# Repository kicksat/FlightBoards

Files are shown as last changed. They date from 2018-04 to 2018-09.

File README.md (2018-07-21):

# mainboard
<p align="middle">
Main PCB driving the Kicksat-2 cubesat mothership. Its job is to depoly Sprites, which looks kind  of like this:
  </br>
</br>
Benchtop development hardware looks like this:
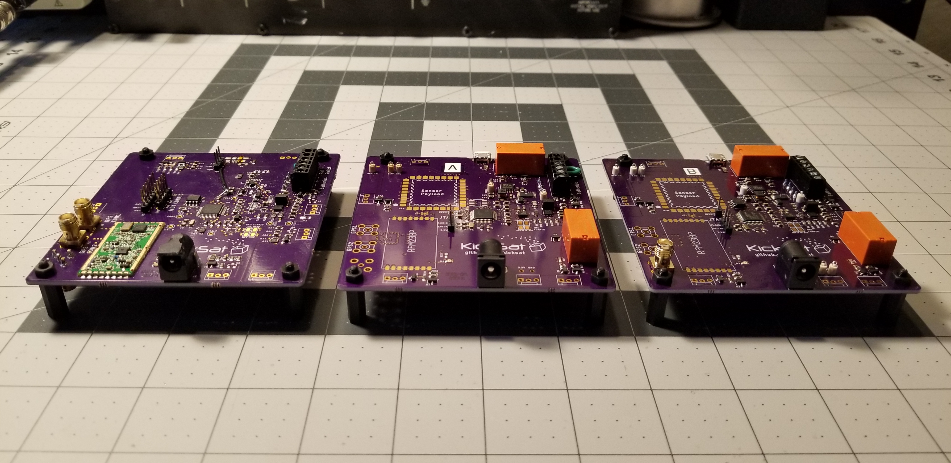
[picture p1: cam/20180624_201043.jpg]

</p>

# License

[Creative Commons Attribution-ShareAlike 4.0 International](https://creativecommons.org/licenses/by-sa/4.0/)

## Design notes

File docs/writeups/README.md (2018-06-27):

## Burnwire hardware block diagram
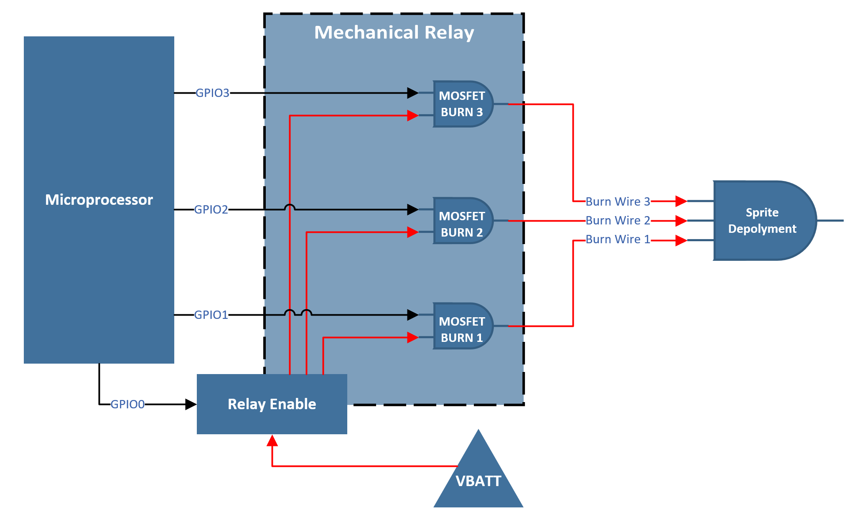
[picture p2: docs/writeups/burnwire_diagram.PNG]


## Burnwire schematic diagram
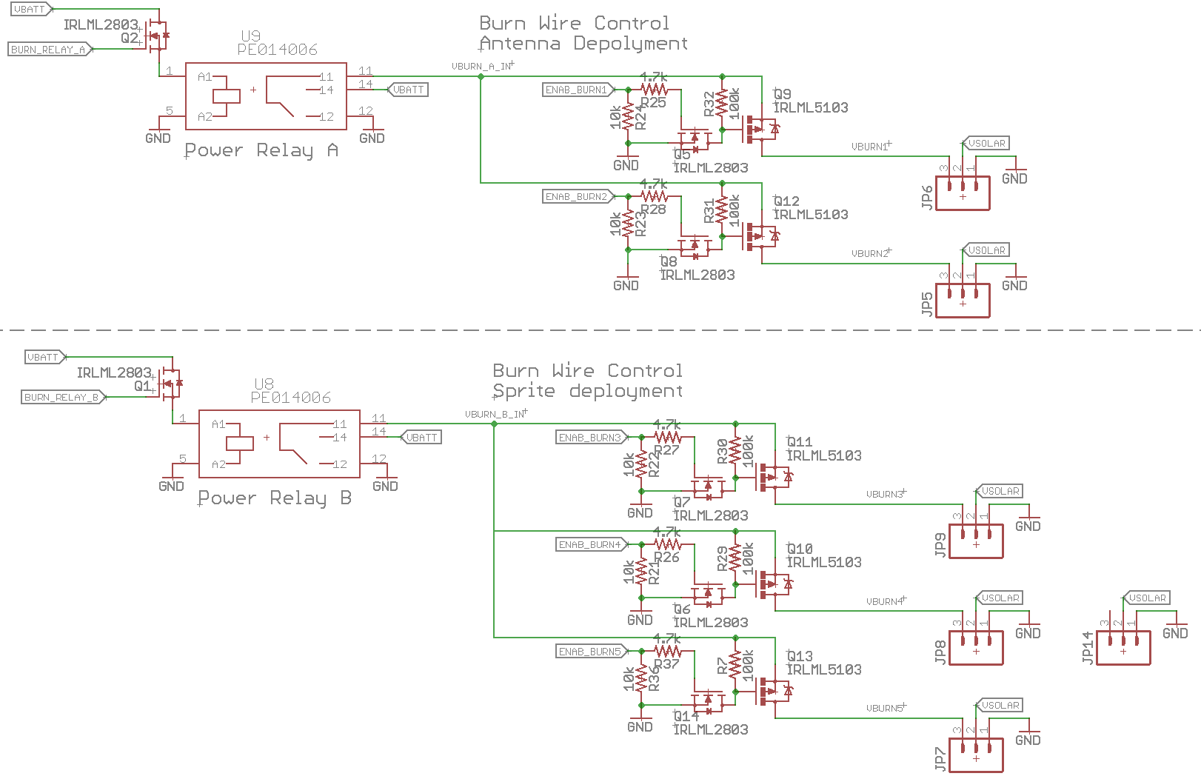
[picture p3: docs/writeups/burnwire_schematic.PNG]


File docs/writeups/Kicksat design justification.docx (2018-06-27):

Kicksat-2 Design Architecture

Radiation Evaluation

Kicksat-2 hardware was designed with a “careful COTS” methodology to ensure mission requirements while optimizing lifetime, capability, and component cost/availability. This approach leverages existing component radiation testing literature with detailed environmental modeling to drive IC component selection.

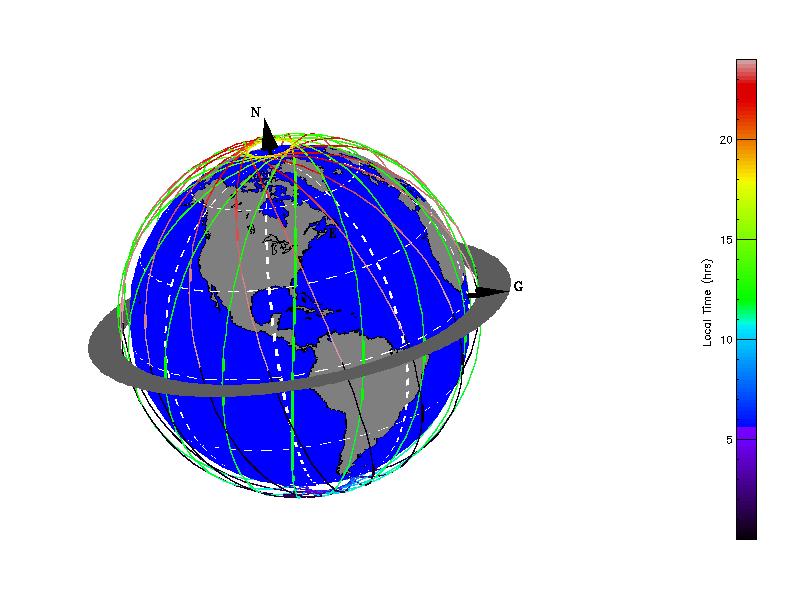
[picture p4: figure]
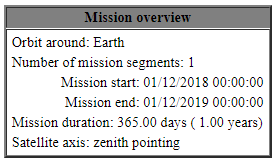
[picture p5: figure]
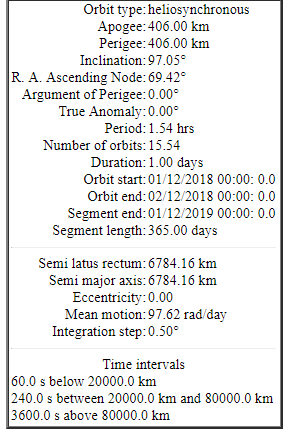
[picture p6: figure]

Environment Simulation:

Figure 1

The ESA Space ENVironment Information System (SPENVIS) was used to generate high-level orbital parameters and subsequent radiation models. Further analysis was then performed using raw AE9/AP9 data in conjunction with Geant4, COMSOL, and VisualTCAD tools to model the anticipated radiation effects. Relevant SPEVIS input parameters used in orbital generation, and a graphical representation of a 24 hour orbital path are shown in Figure _____.

Using the parameters from Figure ____, a standalone copy of AE9/AP9 v1.50 was used to generate trapped particle data. Kicksat-2 mission altitude dictates that total ionizing dose (TID) accumulation will predominately come from trapped particles (electrons and protons). Single event effects (SEE), however, must still be considered since Kicksat-2 must not allow premature Sprite deployment.

Table I | Integrated Circuit Component Summary

P/N | Manufacturer | Function | Mission Critical? | Flight Heritage? | Radiation Test Data?
IRLML2803 | Infineon | N-channel MOSFET | Yes | Unknown | Yes
IRLML5103 | Infineon | P-channel MOSFET | Yes | Unknown | Yes
MAX706R | Maxim | Watchdog Timer | Yes | Yes | Yes
TPS54226 | TI | Regulator | Yes | Yes | Yes
RFM23BP | HopeRF | Radio Transceiver | Yes | Yes | No
MR25H40 | Everspin | Nonvolatile Memory | Yes | Yes | Yes
ATSAMD21G-A | Microchip | Microprocessor | Yes | Unknown | No
PE014006 | TE Connectivity | Mechanical Relay | Yes | No | No
S1216V8 | SkyTraq | GPS Module | No | Yes | No
LSM9DS1 | STMicro | IMU | No | Yes | No
MAX4372TEUK+T | Maxim | Current Sensor | No | Yes | No
LTC4121-4.2 | Analog Devices | Battery Charger | No | No | No
EP2W+ | Mini Circuits | RF Splitter | No | Unknown | No
TY1003 | Tyndall Works | Dosimeter | No | Yes | Yes

Discussion of Critical Components:

IRLML2803 & IRLML5103 – Power MOSFET

MOSFETs have well-documented electrical behavior in radiation environments. Incremental degradation due to ionizing radiation (TID) generally manifests as a decrease in gate threshold voltage for NMOS devices and an increase in threshold voltage for PMOS. Since discrete MOSFET devices play a critical role in the Kicksat burn-wire design, components with extensive radiation characterization were chosen and combined with multiple failsafes to ensure safe Sprite deployment.

Both the IRLML5103 and IRLML2803 were evaluated by O’Bryan et al. in 2001 for TID tolerance using the NSWC Crain facilities [XX]. Testing with the MIL-STD883 1019.8 procedure, including biased and unbiased conditions, the data shows the IRLML5103 has a TID tolerance greater than 35 krad, and the IRLML2803 greater than 30 krad. Both values far exceed the projected mission dose, and O’Bryan et al. has a strong testing track-record in the radiation effects community.

Device failure due to single event effects (SEE) such as burnout and latch-up are not relevant for the burn-wire design because the circuit sits dormant behind the mechanical relay circuit during nearly the entire mission. By protecting the burn-wire circuit with the mechanical relay, there is no bias across the MOSFET devices, thereby preventing an ionizing particle from creating parasitic effects within the channel/bulk regions and causing permeant damage.

MAX706R – Watchdog Timer

The MAX70X series of microprocessor supervisors have an extensive radiation test history covering TID, SEE, and SEL scenarios from a number of researchers [XX – XX]. As reported by Aaron et al, the MAX70X devices have a TID threshold of roughly 11 krad under worst-case biasing conditions [XX]. Additionally, Allen et al. reports a SEL threshold of 72 LET at 25C and about 68 LET at 85C. Both TID and SEE values are well within the required mission parameters, and failure of the MAX706R watchdog cannot result in the premature deployment of Sprites.

TPS54226 - Regulator

The TPS542XX family of DC-DC converters from Texas Instruments has been evaluated for TID and SEE tolerance by multiple researchers [XX – XX]. Specifically, Cochran et al. reported a TID tolerance of 15 – 20 krad, and Allen et al. reported no destructive SEL events occurring on devices biased at 10V or less and under a variety of temperature conditions. The efficiency of the TPS54226 device coupled the device behavior in radiation environments made it the most reliable choice for the Kicksat mission.

RFM23BP – Radio Module

The HopeRF RFM23BP module is a COTS radio integrated onto a PCB. Based on Silicon Labs’ Si4431 transceiver, which has known flight heritage, the module also contains BJT devices, a N-channel UHF amplifier, a SPDT switch, and an LDO [XX]. Although the flight heritage demonstrates adequate reliability for the Kicksat mission, PCB rework was performed to replace the LDO and SPDT switch with components with better documented radiation tolerance.

MR25H40 – Nonvolatile Memory

The MR25H40 is a 4MB non-voltage memory device constructed from magnetoresistive memory devices. The fundamental operation of magnetoresistive memory makes it inherently more tolerant to TID effects. Cochran et al. reports a TID tolerance of 90 – 100 krad during their 2007 work at Goddard Space Flight Center Radiation Effects Facility [XX]. Additionally, O’Bryan et al. was unable to observe upsets in the device using 89 MeV and 189 MeV protons during their 2007 work at the Indiana University Cyclotron Facility [XX].

The high radiation tolerance of the magnetic memory is used to store mission-critical parameters that are periodically verified and referenced during key mission objectives such as Sprite deployment and configurational backups for the microprocessor.

ATSAMD21G-A - Microprocessor

The Kicksat spacecraft operates from a Microchip SAMD2X family of microprocessor. Although there is no published literature on the radiation tolerance of this device, inferences can be made from Cochran et al., 2008 TID work on a “complex 65nm CMOS microprocessor” [XX]. Using the MIL-STD883 1019.8 test method, Cochran et al. reports no degradation detected up to the maximum tested level of 1000 krad. Furthermore, the ATSAMD21G device now has flight heritage after launching onboard OA-9 within the Brown Space Engineering EQUiSat 1U CubeSat.

The ATSAMD21G was chosen for the Kicksat mission because of its 32-bit ARM Cortex-M0+ architecture, low power consumption, and wide accessibility. The confidence level of the device to perform mission-critical duties was enhanced as described in the ______ section.

PE014006 – Mechanical Relay

The PE014006 relay was added to the design to provide an additional layer of protection from premature Sprite deployment. The power relay is inherently a mechanical device that can only be engaged when enough current is driven across the input terminals to actuate a mechanical switch. It therefore is not susceptible to TID degradation. The construction of the device employs a large isolation distance which also protects the relay from SEE-actuated events.

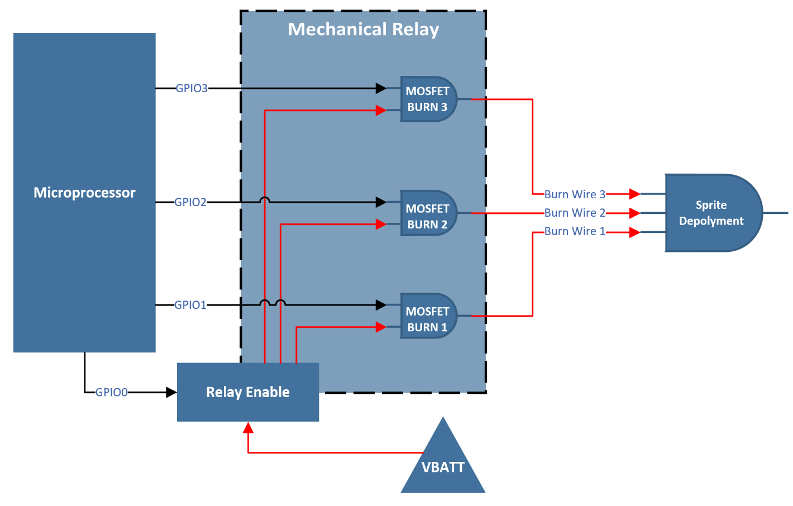
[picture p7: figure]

Sprite Deployment Scheme

Figure 2

The Kicksat-2 deployment scheme employs hardware and software safeguards to prioritize timely Sprite deployment above mission operational parameters, while also addressing detrimental environmental effects such as radiation-induced SEE and transient voltage spikes.

Hardware

Figure ___ and Fig. ____ illustrate the four hardware mechanisms in place to prevent premature deployment. A section of the schematic is also included in Fig. _____ as an alternative method of visualizing the safeguards. It’s important to note that each possible failure mode of the hardware defaults to a no-deployment condition. This hardware includes:

1. Three burnwires must be severed to release the Sprites.
2. Each burnwire circuit is operated by a separate I/O pin on the microprocessor.
3. A mechanical relay is placed in-line within the high-current path from the battery to the burnwires to further safeguard from early deployment by decoupling the electrical and mechanical aspects of the design.
4. An external, radiation tolerant, watchdog timer is used to monitor activity of the microprocessor and can disable all relay and MOSFET actuation if continuous checkpoints are not met.

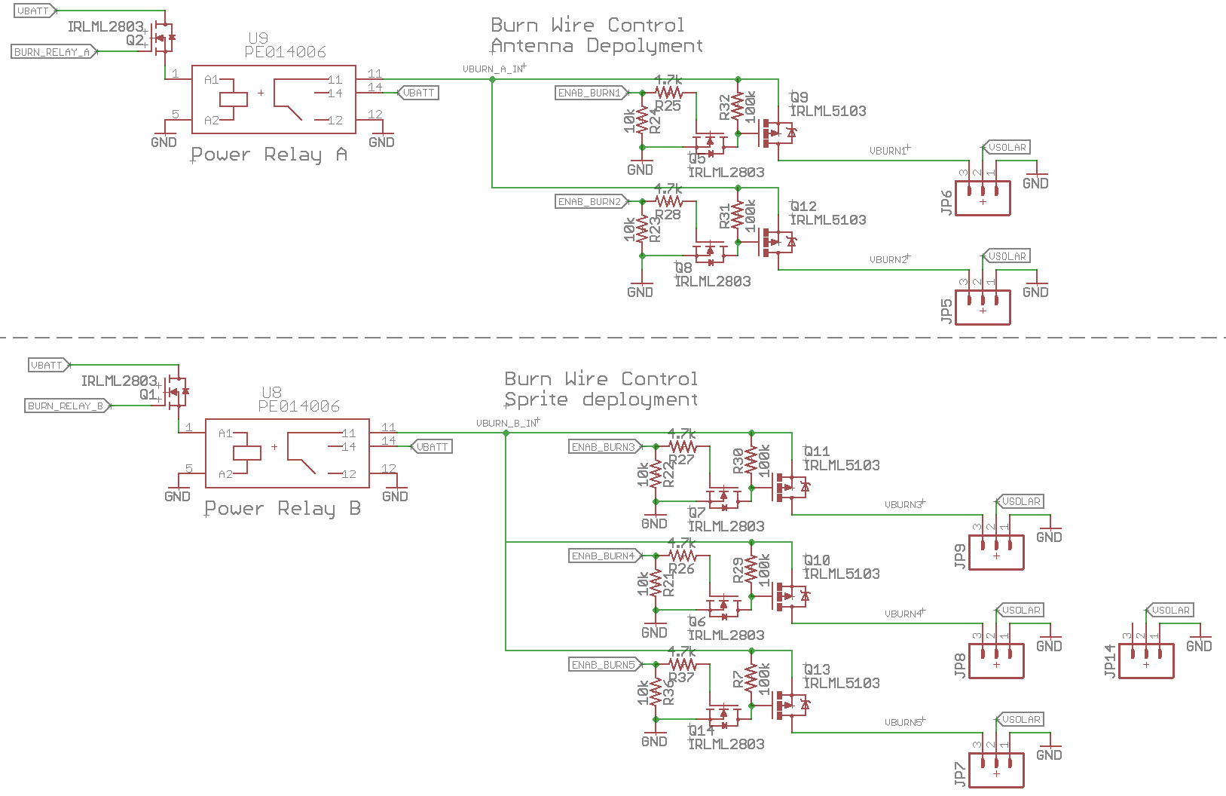
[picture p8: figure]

Figure 3

Software

1. Each software checkpoint is reached via compartmentalized multi-byte strings that contain several Boolean conditions per string. This technique makes the software increasingly more tolerant of radiation-induced bit flips.
2. Kicksat-2 firmware defaults to a no-deployment condition requiring two checkpoints to be reached before entering a valid deployment scenario:
  a. At launch, the software stack does not contain the code necessary to execute a deployment actuation. The deployment-specific software loop is stored on the radiation-tolerant microSD and magnetoresistive memory as a byte string. The deployment-specific loop will then only be read and internalized once a specific ground station command (as described in #1) is received.
  b. The deployment software will begin checking against an internal and GPS-read date/time condition before proceeding.
3. Inadvertent signals on the GPIO pins controlling the redundant burnwire circuit and relay circuits are further protected by leveraging the unique microcontroller SERCOM capability. This silicon-enabled feature allows many of the GPIO to be preconfigured for SPI, I2C, UART, and GPIO states. Relevant burnwire pins are preconfigured to a data-in SPI state, thereby eliminating the possibility HIGH/LOW conditions characteristic of GPIO lines until multiple registers are configured to change the SERCOM state. Only once the pin is configured as a GPIO can it then be brought HIGH and begin the various hardware steps described above.

References:

K. Aaron et al., “Compendium of Recent Total Ionizing Dose Test Results Conducted by the Jet Propulsion Laboratory from 2003 through 2009,” IEEE Radiation Effects Data Workshop, 2009.

G. Allen, “Compendium of Test Results of Single Event Effects Conducted by the Jet Propulsion Laboratory,” IEEE Radiation Effects Data Workshop, 2008.

D. Cochran et al., “Total Ionizing Dose and Displacement Damage Compendium of Candidate Spacecraft Electronics for NASA,” IEEE Radiation Effects Data Workshop, 2009.

G. Allen et al., “Heavy Ion Induced Single-Event Latchup Screening of Integrated Circuits Using Commercial Off-the-Shelf Evaluation Boards,” IEEE Radiation Effects Data Workshop, 2016.

D. Cochran et al., “Compendium of Recent Total Ionizing Dose Results for Candidate Spacecraft Electronics for NASA,” IEEE Radiation Effects Data Workshop, 2008.

O’Bryan et al., “Compendium of Recent Single Event Effects Results for Candidate Spacecraft Electronics for NASA,” IEEE Radiation Effects Data Workshop, 2008.

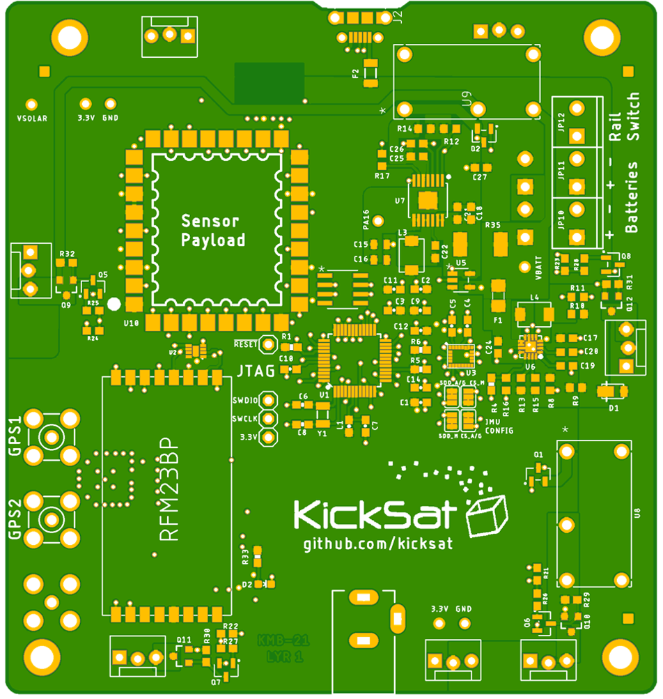
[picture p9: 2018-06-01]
cam/KMB-21.png

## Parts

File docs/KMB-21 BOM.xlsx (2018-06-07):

OSH ORDER 2018-06-04 |  |  | KMB-21.sch at 6/6/2018 5:23 PM
 |  |  |  |  |  | (DK 2018-04-05) | (2*2.1 rounded) | (DK 2018-06-07)
Qty | Value | Device | Package | Parts | Description | Inventory | Total Needed | New Order | Comments
3 | 22uF | 22UF-0805-6.3V-20% | 805 | C15, C16, C24 | 22ÂµF ceramic capacitors | 6 | 13 | 15
4 | 10uF | 10UF-0603-6.3V-20% | 603 | C1, C17, C18, C21 | 10.0ÂµF ceramic capacitors | 95 | 17
3 | 2.2uF | 2.2UF-0603-10V-20% | 603 | C19, C20, C27 | 2.2ÂµF ceramic capacitors | 98 | 13
12 | 0.1uF | 0.1UF-25V(+80/-20%)(0603) | 0603-CAP | C2, C3, C5, C7, C9, C10, C11, C12, C13, C14, C22, C23 | CAP-00810 | 85 | 50
1 | 3.3nF | 3.3NF-0603-100V-10% | 603 | C25 | 3.3nF ceramic capacitors | 8 | 4
1 | 1.0uF | 1.0UF-0603-16V-10% | 603 | C26 | 1ÂµF ceramic capacitors | 98 | 4
1 | 10nF | 10NF/10000PF-50V-10%(0603) | 0603-CAP | C4 | CAP-00867 | 99 | 4
2 | 15pF | 15PF-50V-5%(0603) | 0603-CAP@1 | C6, C8 | CAP-07881 | 98 | 8
1 | DFLS130L | DFLS130L | PWRDI-123 | D1 |  | 9 | 4
1 | GREEN | LED-GREEN0603 | LED-0603 | D2 | Various green LEDs | 0 | 4 | 10
1 | 1206L200 | PTCFUSE1206 | 1206 | F1 | PTC Fuse | 9 | 4
1 | 500mA | PTCSMD | PTC-1206 | F2 | Resettable Fuse PTC | 9 | 4
1 | 503182-1852 | 503182-1852 | MOLEX_503182-1852 | J1 | Conn Micro SD Card M 8 POS 1.09mm Solder RA SMD Embossed T/R 0.5A/Contact | 0 | 4 | 10
1 | 10118194-0001LF | 10118194-0001LF | FRAMATOME_10118194-0001LF | J2 | Conn Micro USB Type B RCP 5 POS 0.65mm Solder RA SMD 5 Terminal 1 Port T/R | 0 | 4 | 25
1 | DCJ0303 | DCJ0303 | DCJ0303 | J3 | DC POWER JACK | 0 | 4 | 10
5 | M023.5MM_LOCK | M023.5MM_LOCK | SCREWTERMINAL-3.5MM-2_LOCK | JP10, JP11, JP12, JP13, JP16 | Standard 2-pin 0.1" header. Use with | 45 | 21
7 |  | M03POLAR_LOCK | MOLEX-1X3_LOCK | JP5, JP6, JP8, JP9, JP14, JP15, JP17 | Header 3 | 100 | 29
1 | FB - 30Ohm | INDUCTOR0603 | 603 | L1 | Inductors | 8 | 4
1 | 3.3uH | IND1812 | 1812 | L3 |  | 2 | 4 | 0 | Decent inductors are restricted on digikey? Need to go to Mouser?
1 | 56uH | IND1812 | 1812 | L4 |  | 4 | 4
7 | IRLML2803 | IRLML2803TRPBF | SOT-23 | Q1, Q2, Q3, Q5, Q6, Q7, Q8 |  | 5 | 29 | 50
5 | IRLML5103 | MOSFET-PCHANNEL | SOT23-3 | Q4, Q9, Q10, Q11, Q12 | Generic PMOSFET | 4 | 21 | 50
8 | 10K | 10KOHM-1/10W-1%(0603)0603 | 0603-RES | R1, R4, R18, R21, R22, R23, R24, R34 | RES-00824 | 0 | 34 | 100
1 | 330K | R-US_R0603 | R0603 | R10 | RESISTOR, American symbol | 99 | 4
1 | 43K | R-US_R0603 | R0603 | R11 | RESISTOR, American symbol | 99 | 4
1 | 73.2K | R-US_R0603 | R0603 | R12 | RESISTOR, American symbol | 0 | 4 | 20
1 | 470k | R-US_R0603 | R0603 | R13 | RESISTOR, American symbol | 99 | 4
1 | 22.1k | R-US_R0603 | R0603 | R14 | RESISTOR, American symbol | 0 | 4 | 20
1 | 6.04K | R-US_R0603 | R0603 | R16 | RESISTOR, American symbol | 99 | 4
8 | 4.7k | R-US_R0603 | R0603 | R2, R3, R15, R19, R25, R26, R27, R28 | RESISTOR, American symbol | 0 | 34 | 100
1 | 3.3K | R-US_R0603 | R0603 | R20 | RESISTOR, American symbol | 99 | 4
6 | 100k | RESISTOR0603 | 603 | R8, R17, R29, R30, R31, R32 | Generic Resistor Package | 0 | 25 | 100
1 | 330 | 330OHM1/10W1%(0603) | 0603-RES | R33 | RES-00818 | 0 | 4 | 100
1 | 0.025 | R-US_R2512 | R2512 | R35 | RESISTOR, American symbol | 0 | 4 | 5
1 | 110K | 10KOHM-1/10W-1%(0603)0603 | 0603-RES | R5 | RES-00824 | 99 | 4
1 | 316K | 10KOHM-1/10W-1%(0603)0603 | 0603-RES | R6 | RES-00824 | 99 | 4
1 | 40.9K | R-US_R0603 | R0603 | R9 | RESISTOR, American symbol | 0 | 4 | 100
1 | MAX706R | MAX708RESA-T | SO8 | U1 |  | 0 | 4 | 5
1 | EP2W+ | EP2W+ | QFN32-5X5MM | U12 |  | 0 | 4 | 0
1 | RFM23BP | RFM23BP | RFM23BP | U13 | HopeRF RFM23BP | 0 | 4 | 0
1 | S1216V8 | S1216V8 | S1216_24PIN_PACKAGE | U14 |  | 0 | 4 | 0
1 | MR25H40 | MR25H40 | DFN-8 | U2 |  | 0 | 4 | 2 | Expensive
1 | LSM9DS1 | LSM9DS1 | LGA24-8X4 | U3 | LSM9DS1 3D accelerometer, gyroscope & magnetometer | 9 | 4
1 | ATSAMD21G-A | ATSAMD21G-A | TQFP-48 | U4 | Atmel SAMD21G SMART ARM-Based Microcontroller | 8 | 4
1 | MAX4372TEUK+T | MAX4372TEUK+T | 21-0057F | U5 |  | 8 | 4
1 | LTC4121-4.2 | LTC4121-4.2 | QFN-16-PAD | U6 |  | 4 | 4
1 | TPS54226PWPRPWP14_2P31X2P46-L | TPS54226PWPRPWP14_2P31X2P46-L | PWP14_2P31X2P46-L | U7 |  | 6 | 4
2 | PE014006 | PE014005 | RELAY5-PE_CO | U8, U9 |  | 0 | 8 | 10
3 | BU-SMA-V | BU-SMA-V | BU-SMA-V | X1, X2, X3 | FEMALE SMA CONNECTOR | 7 | 13 | 0
1 | 32.768kHz | CRYSTAL3.2X1.5MM | CRYSTAL-SMD-3.2X1.5MM | Y1 | Various standard crystals. Proven footprints. | 9 | 4
NON PCB ITEMS
3 | 4GB | S304TLN7B-U1000-3 |  |  | Flash Memory Card, MicroSDHC Card, UHS-1, Class 10, 4 GB, U331 Series | 0 | 1 | 0 | 56 ea from Newark http://www.newark.com/delkin-devices/s304tln7b-u1000-3/memory-card-microsdhc-slc-4gb/dp/37AC8587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

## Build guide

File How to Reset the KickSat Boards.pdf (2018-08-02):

How to Reset the KickSat Boards:

1) Connect ground to RESET
2) Tap it twice quickly
3) If you are doing this quickly, the LED will blink when you tap the reset pin

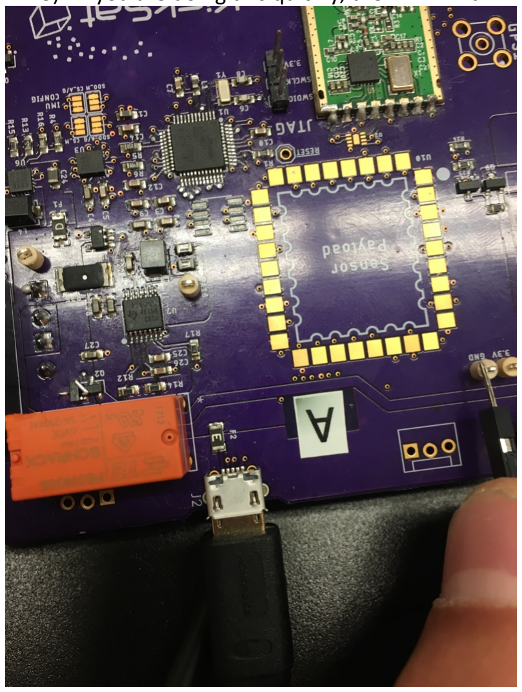
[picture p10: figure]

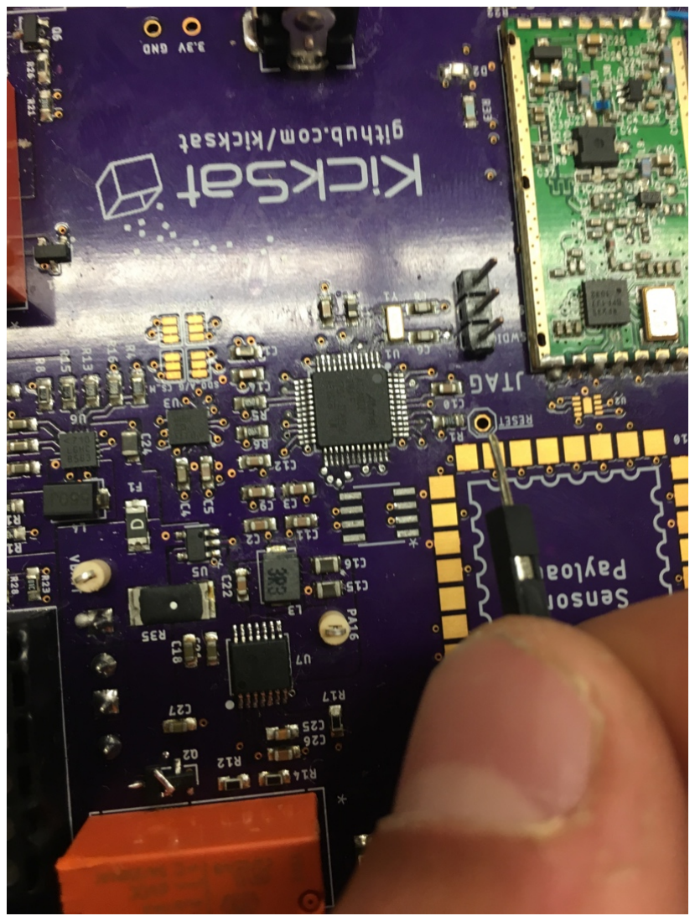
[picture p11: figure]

Reset on Board A:

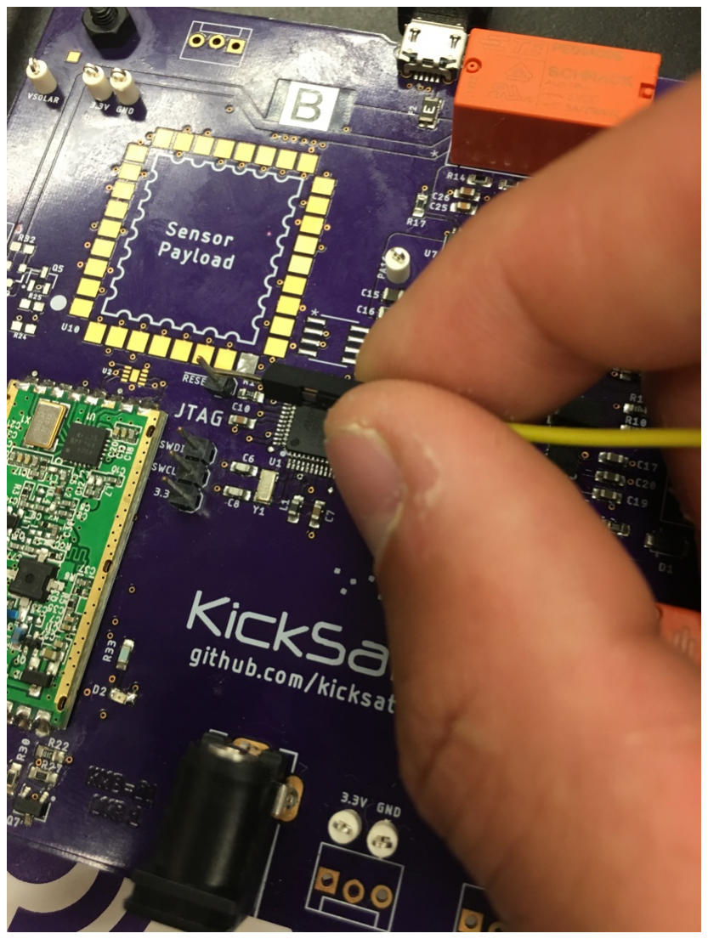
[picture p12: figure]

Reset on Board B

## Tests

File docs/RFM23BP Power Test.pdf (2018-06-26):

Page 1

Power Output versus Voltage – RFM22B and RFM23BP PCB - ¼ Wave antenna
RFM22 on regulated 3V3 supply, RFM23BP direct on battery
Voltage | 3.0 | 3.2 | 3.4 | 3.6 | 3.8 | 4.0 | 4.2 | 4.4 | 4.6 | 4.8 | 5.0
RFM22B – Power -dBm | -44.5 -43.5 | -43 -42.5 -42.5 -41.5 -41.5 -41.5 -41.5 -41.5 -41.5
| 100 | 110 | 115 | 120 | 130 | 130 | 130 | 130 | 130 | 130 | 130
-38.5 | -37 -36.5 | -36 -35.5 -34.5 | -34 -33.5 -33.5 -33.5 -33.5
| 310 | 360 | 400 | 450 | 510 | 530 | 550 | 560 | 580 | 590 | 600
| 210 | | | | | 340 | | | | | 360
| -44.5 | | | | | -37 | | | | | -36

RFM22B – Current mA

RFM23B – Power -dBm – max power RFM23B – Current mA – max power

RFM23B – Current mA – min power RFM23B – Power idBm – min power

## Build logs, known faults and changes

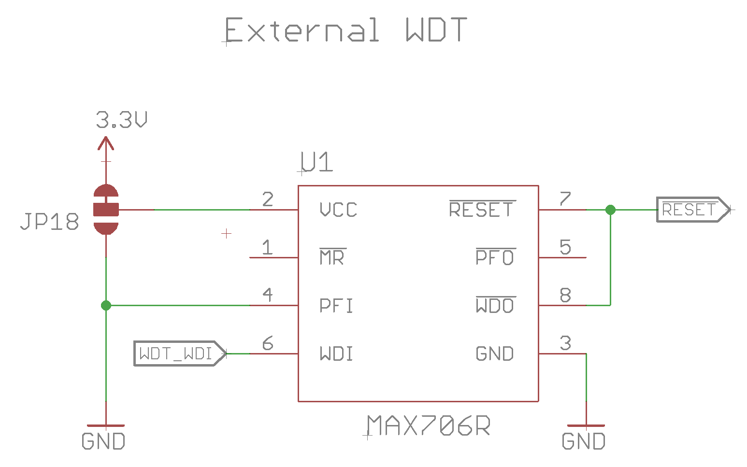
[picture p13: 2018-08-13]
past revisions/KMB-22/WDT_Sch.PNG

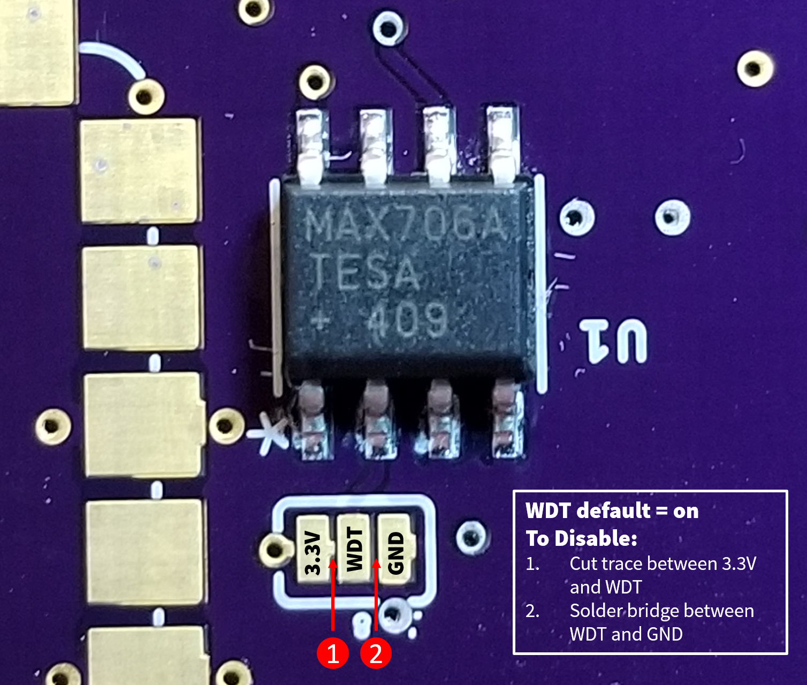
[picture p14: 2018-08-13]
past revisions/KMB-22/WDT_Disable.PNG

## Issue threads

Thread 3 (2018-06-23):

NASA PSRP request - additional burn wire

maholli, 2018-06-23:

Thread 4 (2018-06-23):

Verify KMB-21 Lipo charging circuit

maholli, 2018-06-23:

maholli, 2018-08-04:
@pmathikshara and and I worked on KMB-21A and demonstrated there is an additional resistor divider needed to set the proper float voltage for the charging IC.
- [ ] need to make board modifications and then test charging the 2s2p packs

maholli, 2018-08-06:
Board mods are (mostly) done. The resistor diviers needed to set the charging voltage need to have quite a tight tolerance. I've ordered the resistors.

This will be on hold until the resistors arrive.

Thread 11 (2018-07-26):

KMB-20/21 Rework

maholli, 2018-07-26:
- [x] Reattach USB and on KMB-20
- [x] Remove new solder bridge on KMB-20
- [x] Replace SAMD21 on KMB-21B

Closed 2018-08-06.

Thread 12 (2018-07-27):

modify KMB-20 board for mechanical burn-wire testing

maholli, 2018-07-27:

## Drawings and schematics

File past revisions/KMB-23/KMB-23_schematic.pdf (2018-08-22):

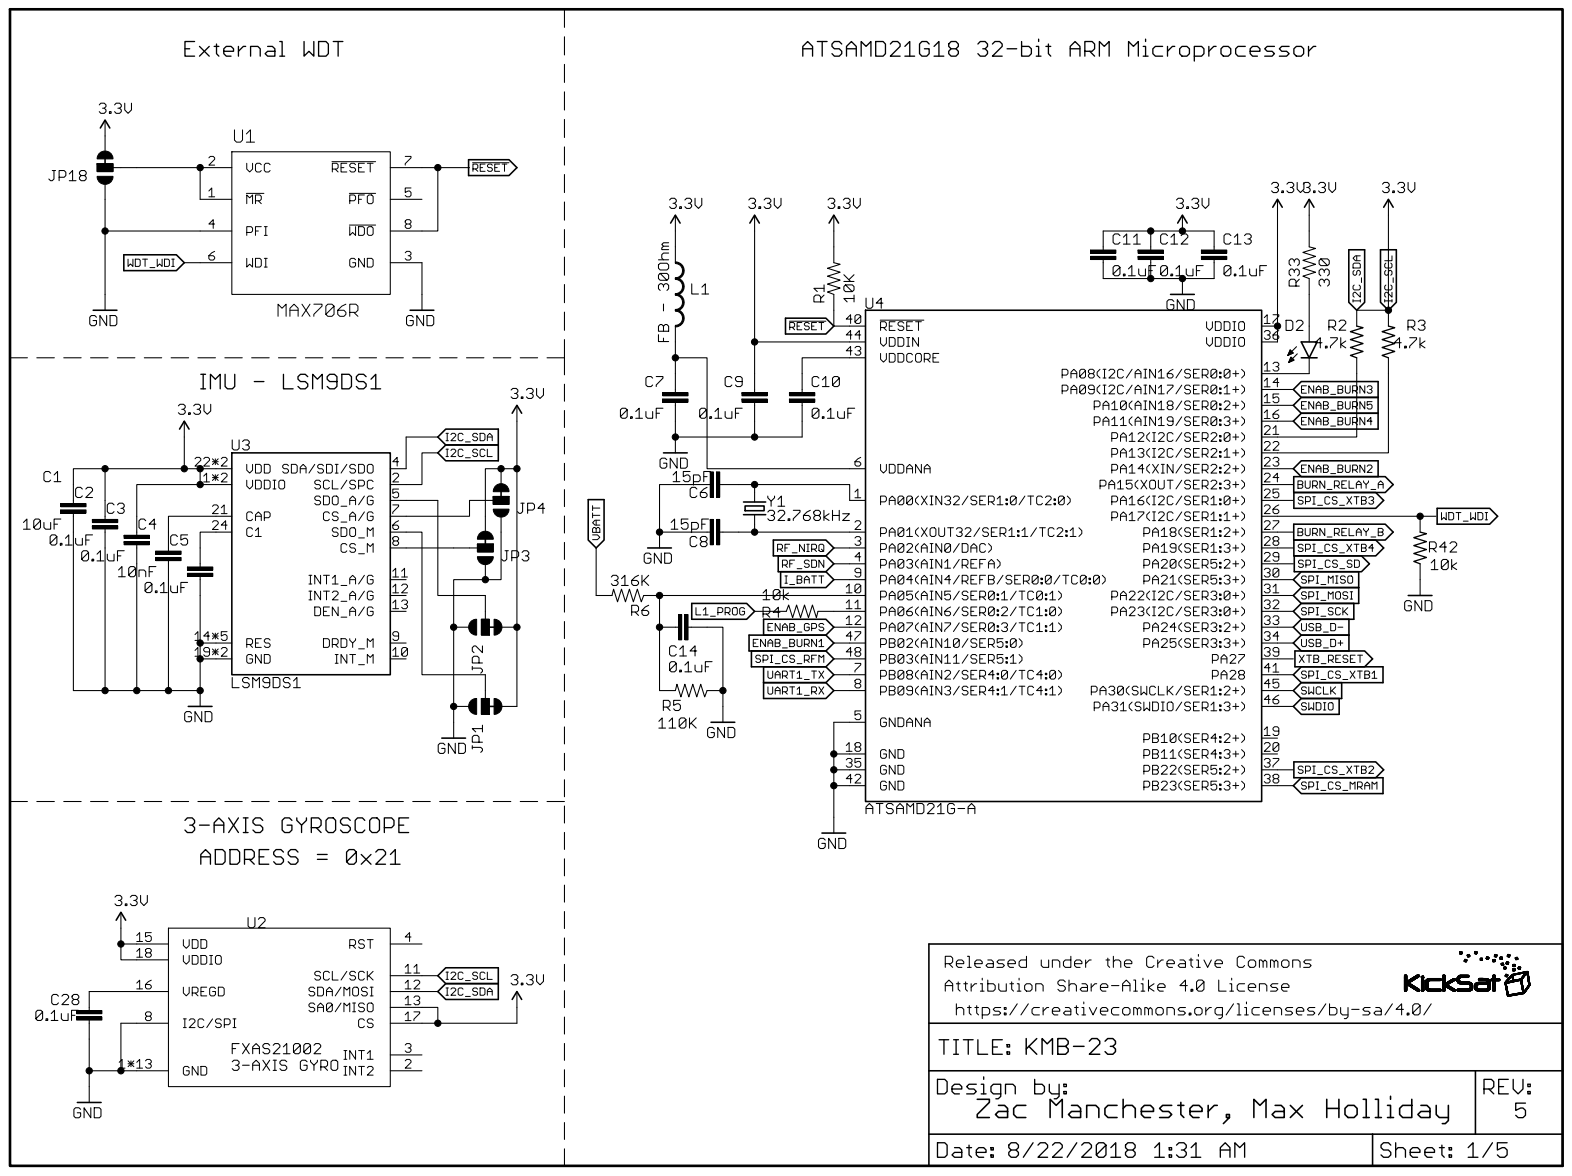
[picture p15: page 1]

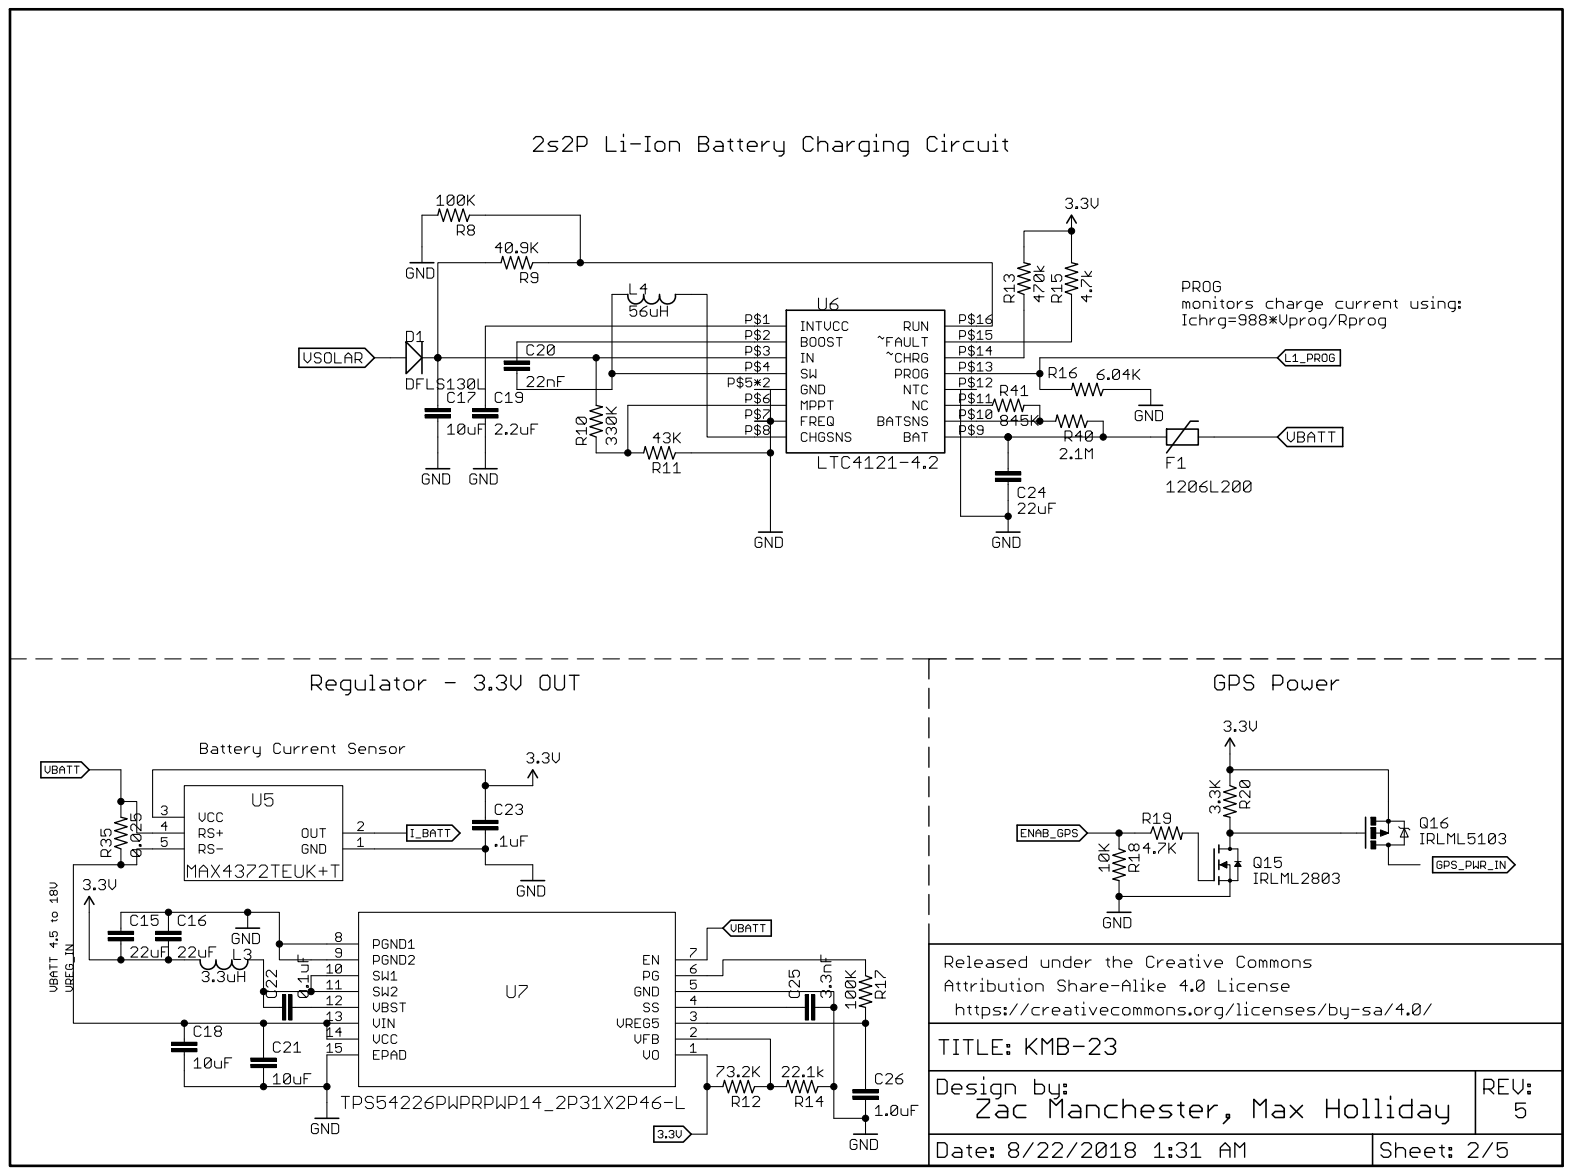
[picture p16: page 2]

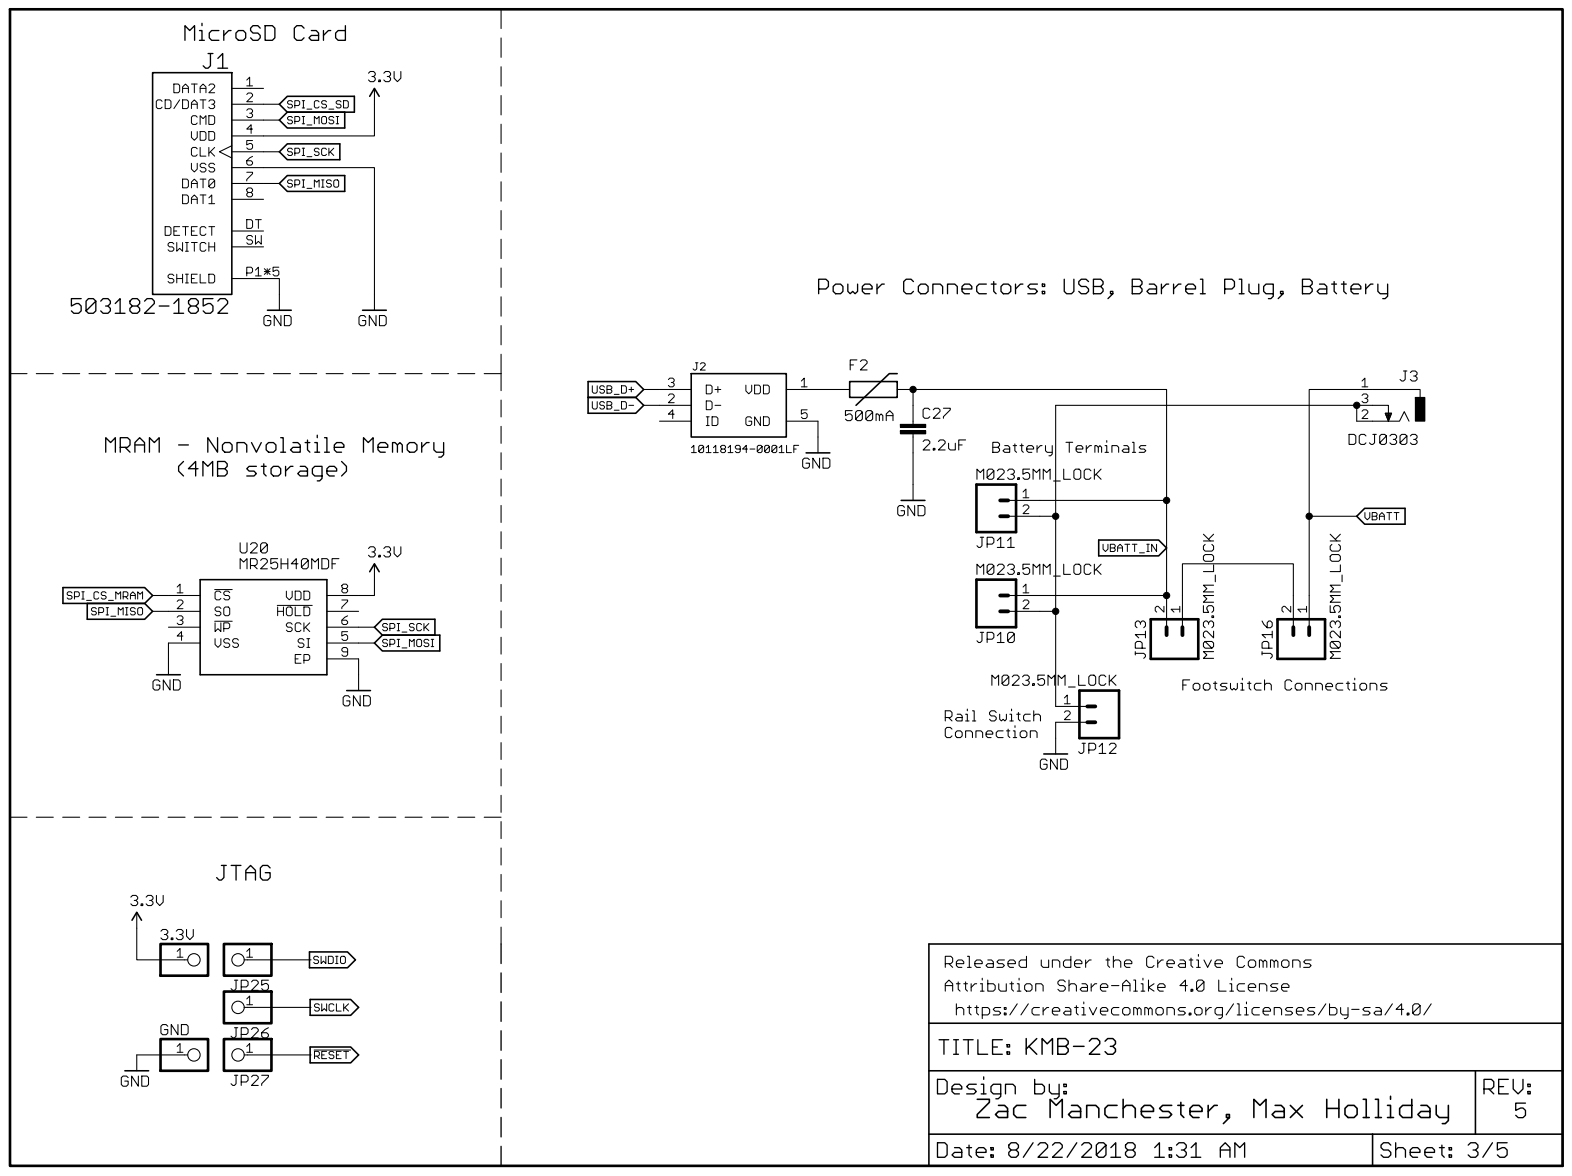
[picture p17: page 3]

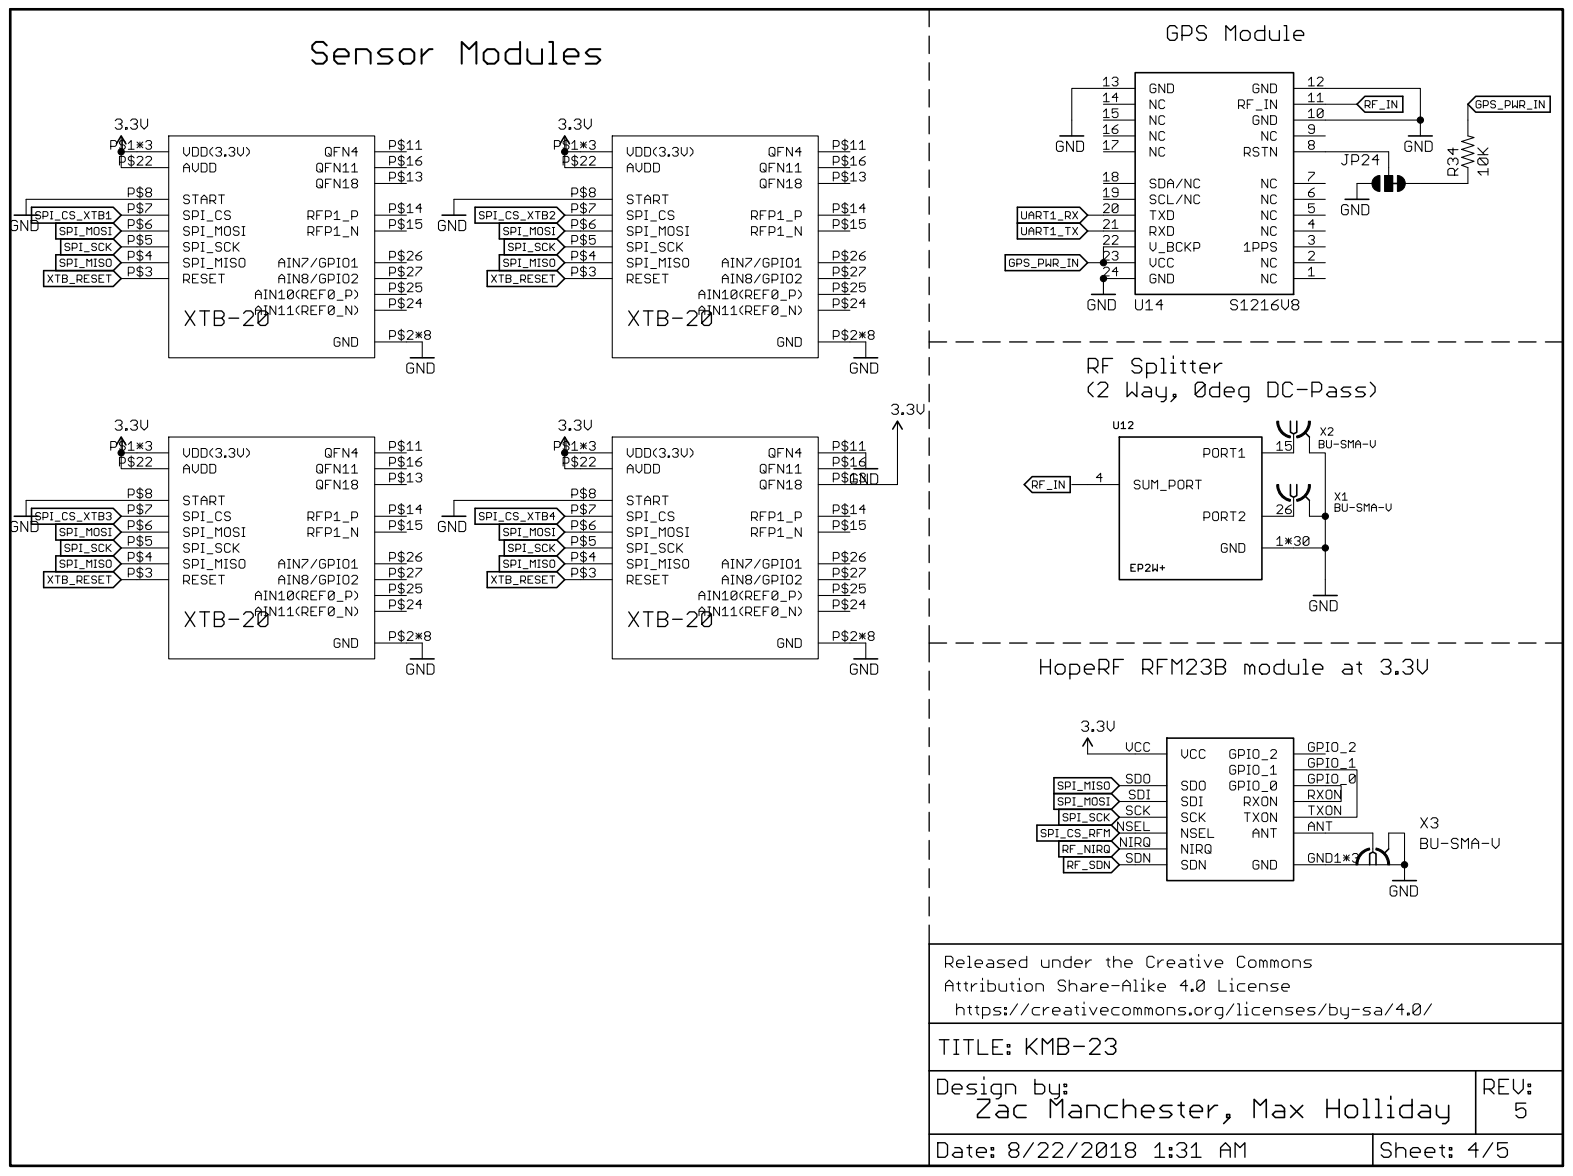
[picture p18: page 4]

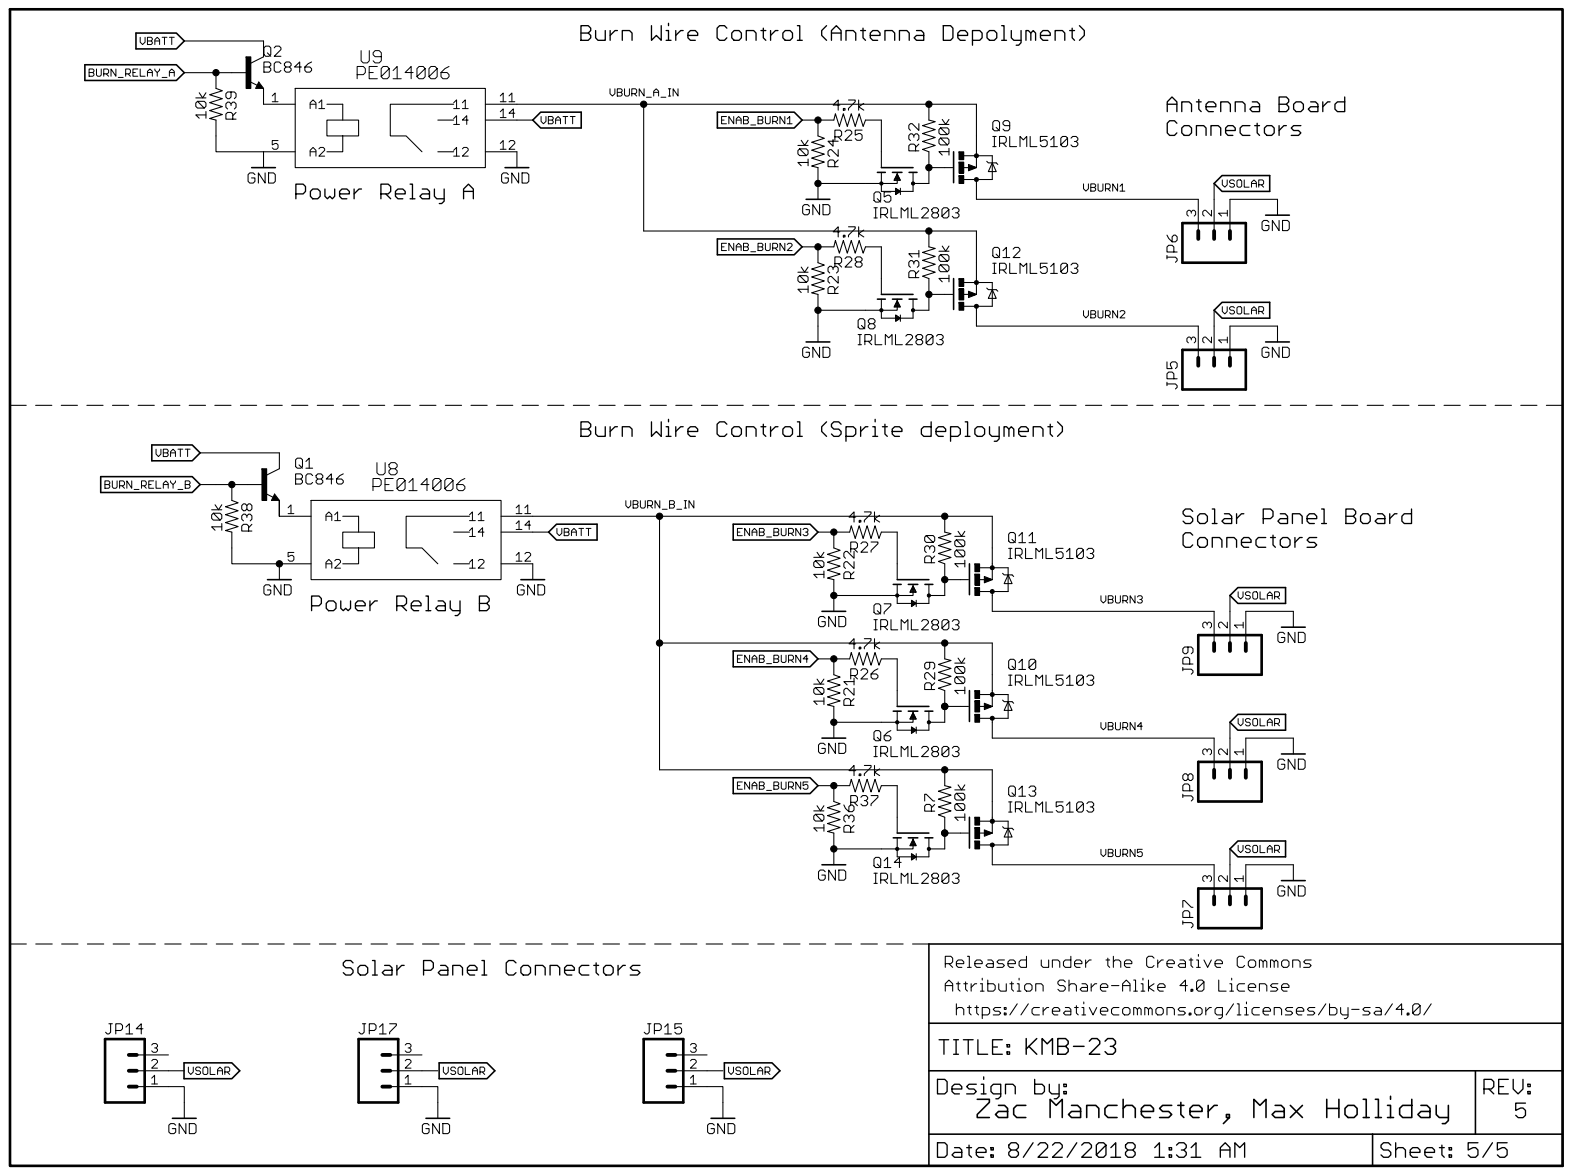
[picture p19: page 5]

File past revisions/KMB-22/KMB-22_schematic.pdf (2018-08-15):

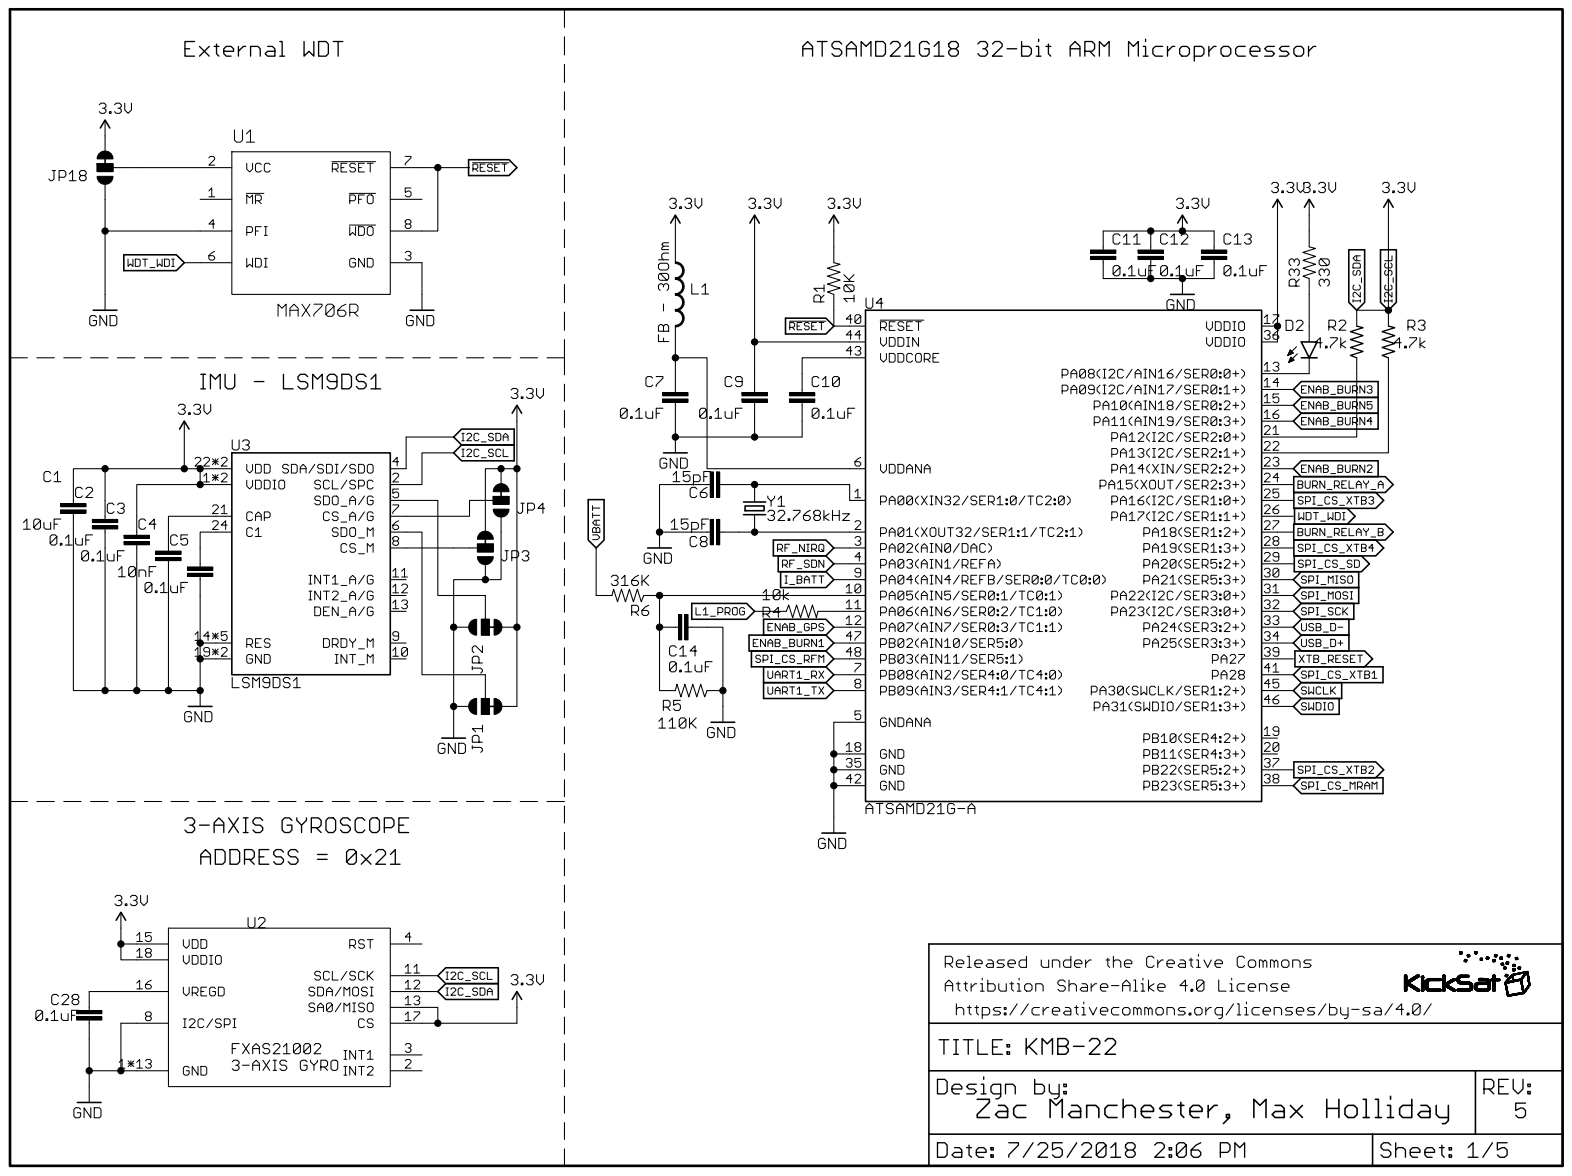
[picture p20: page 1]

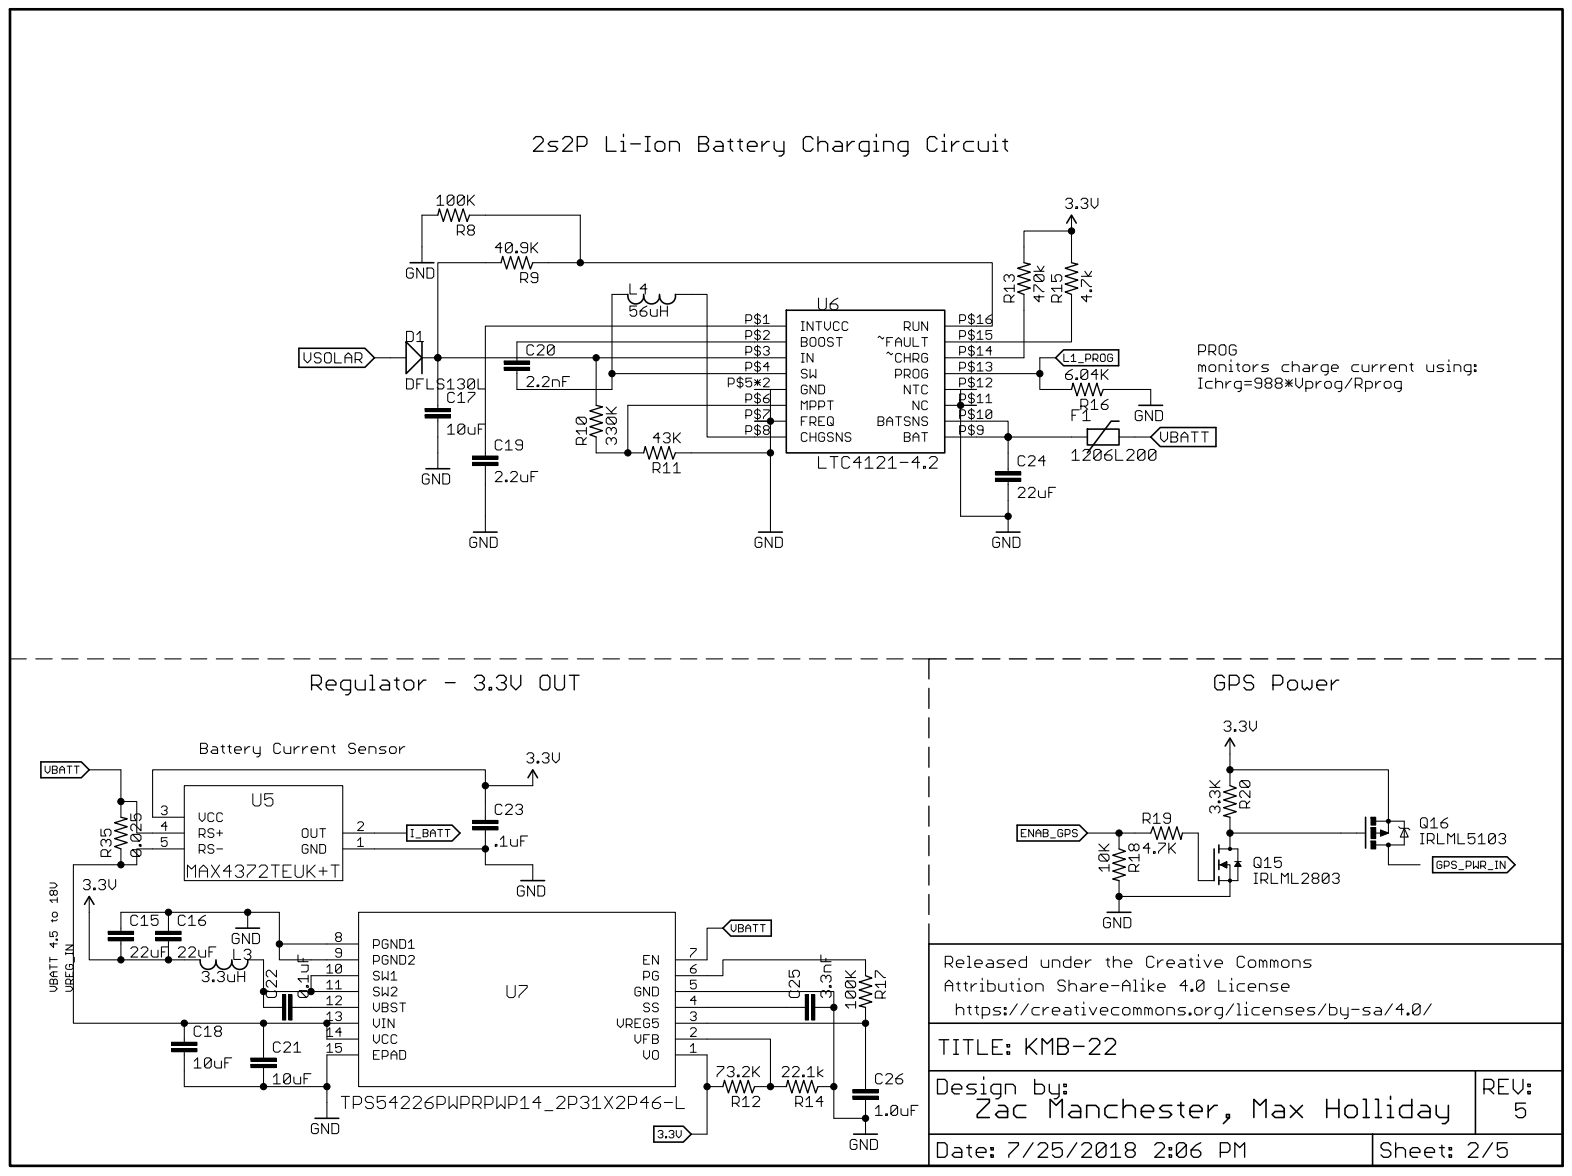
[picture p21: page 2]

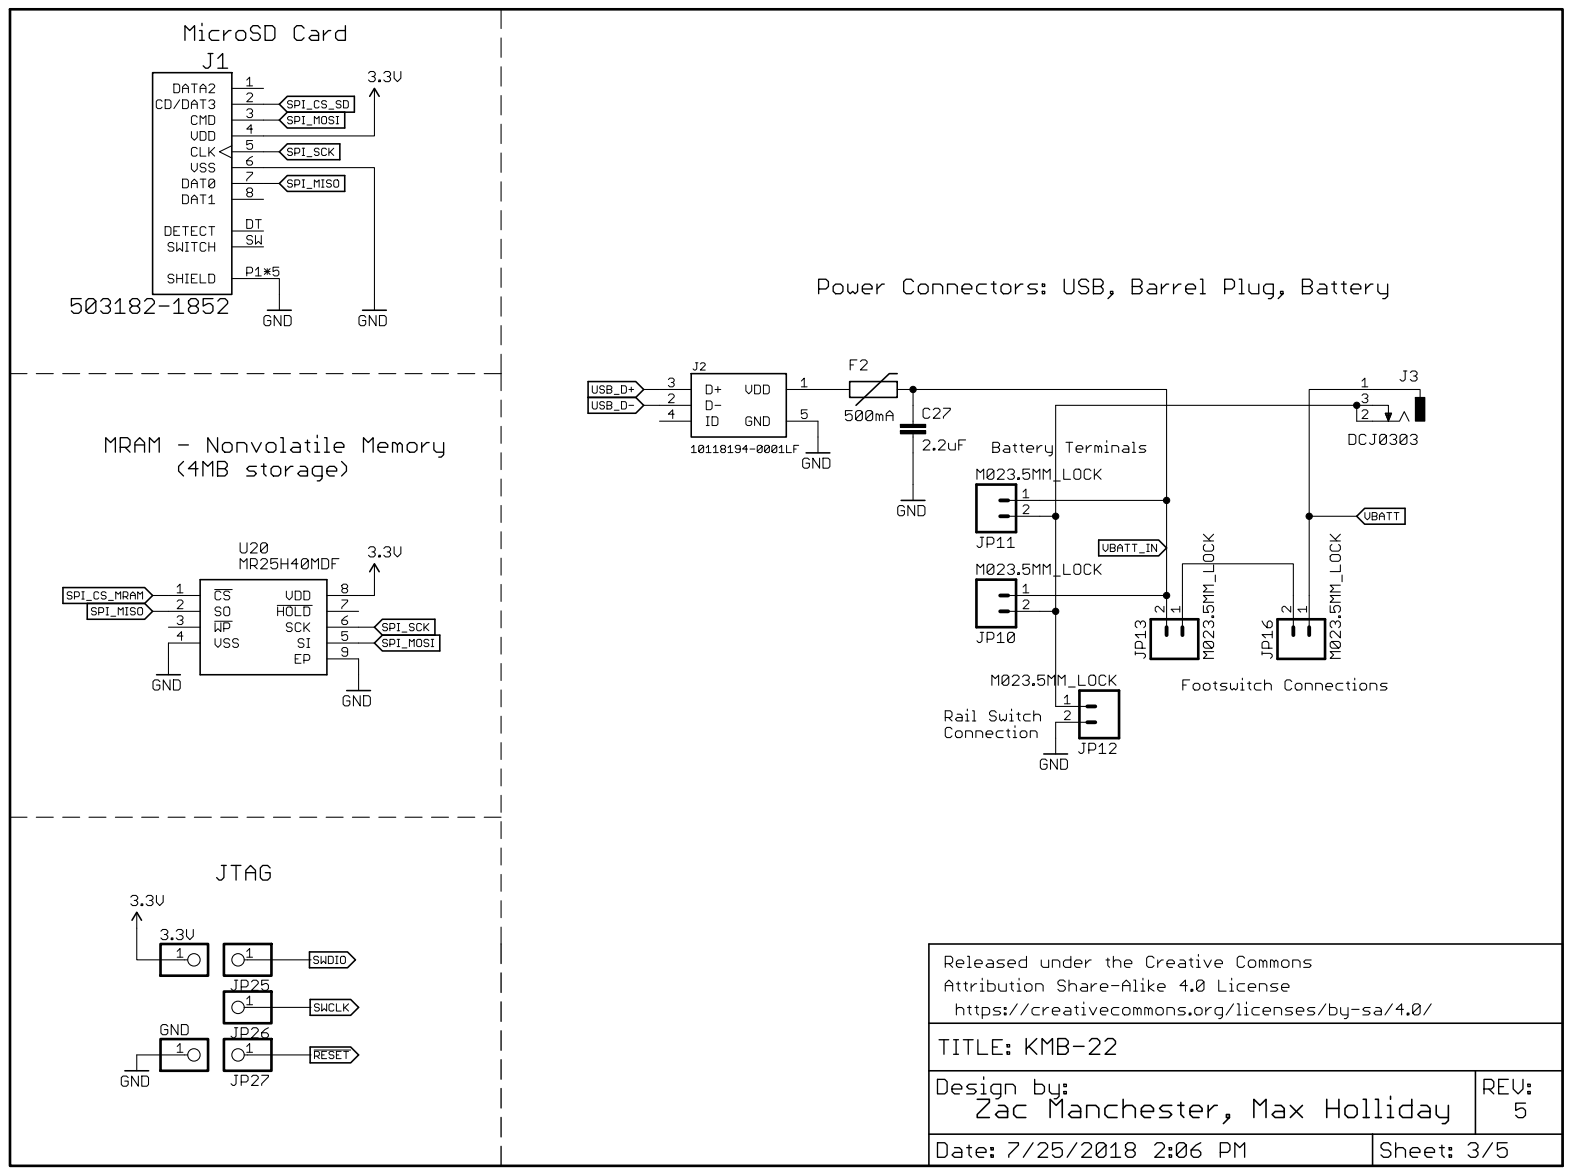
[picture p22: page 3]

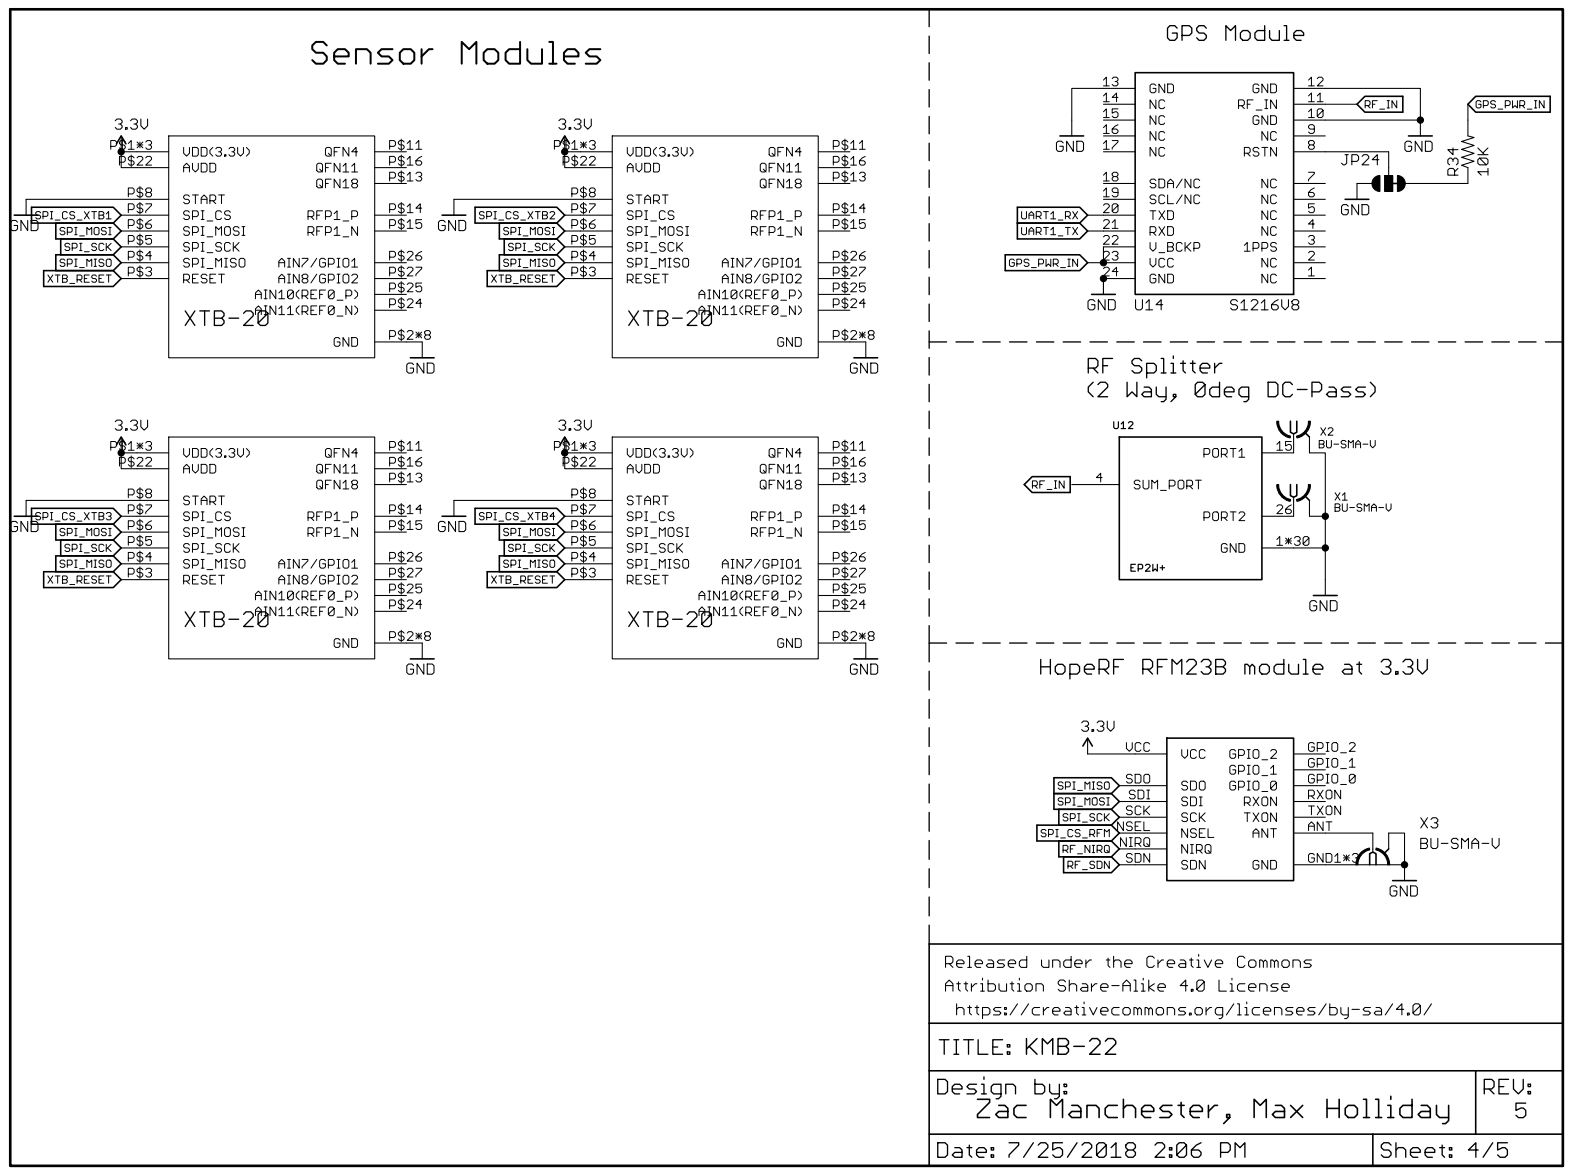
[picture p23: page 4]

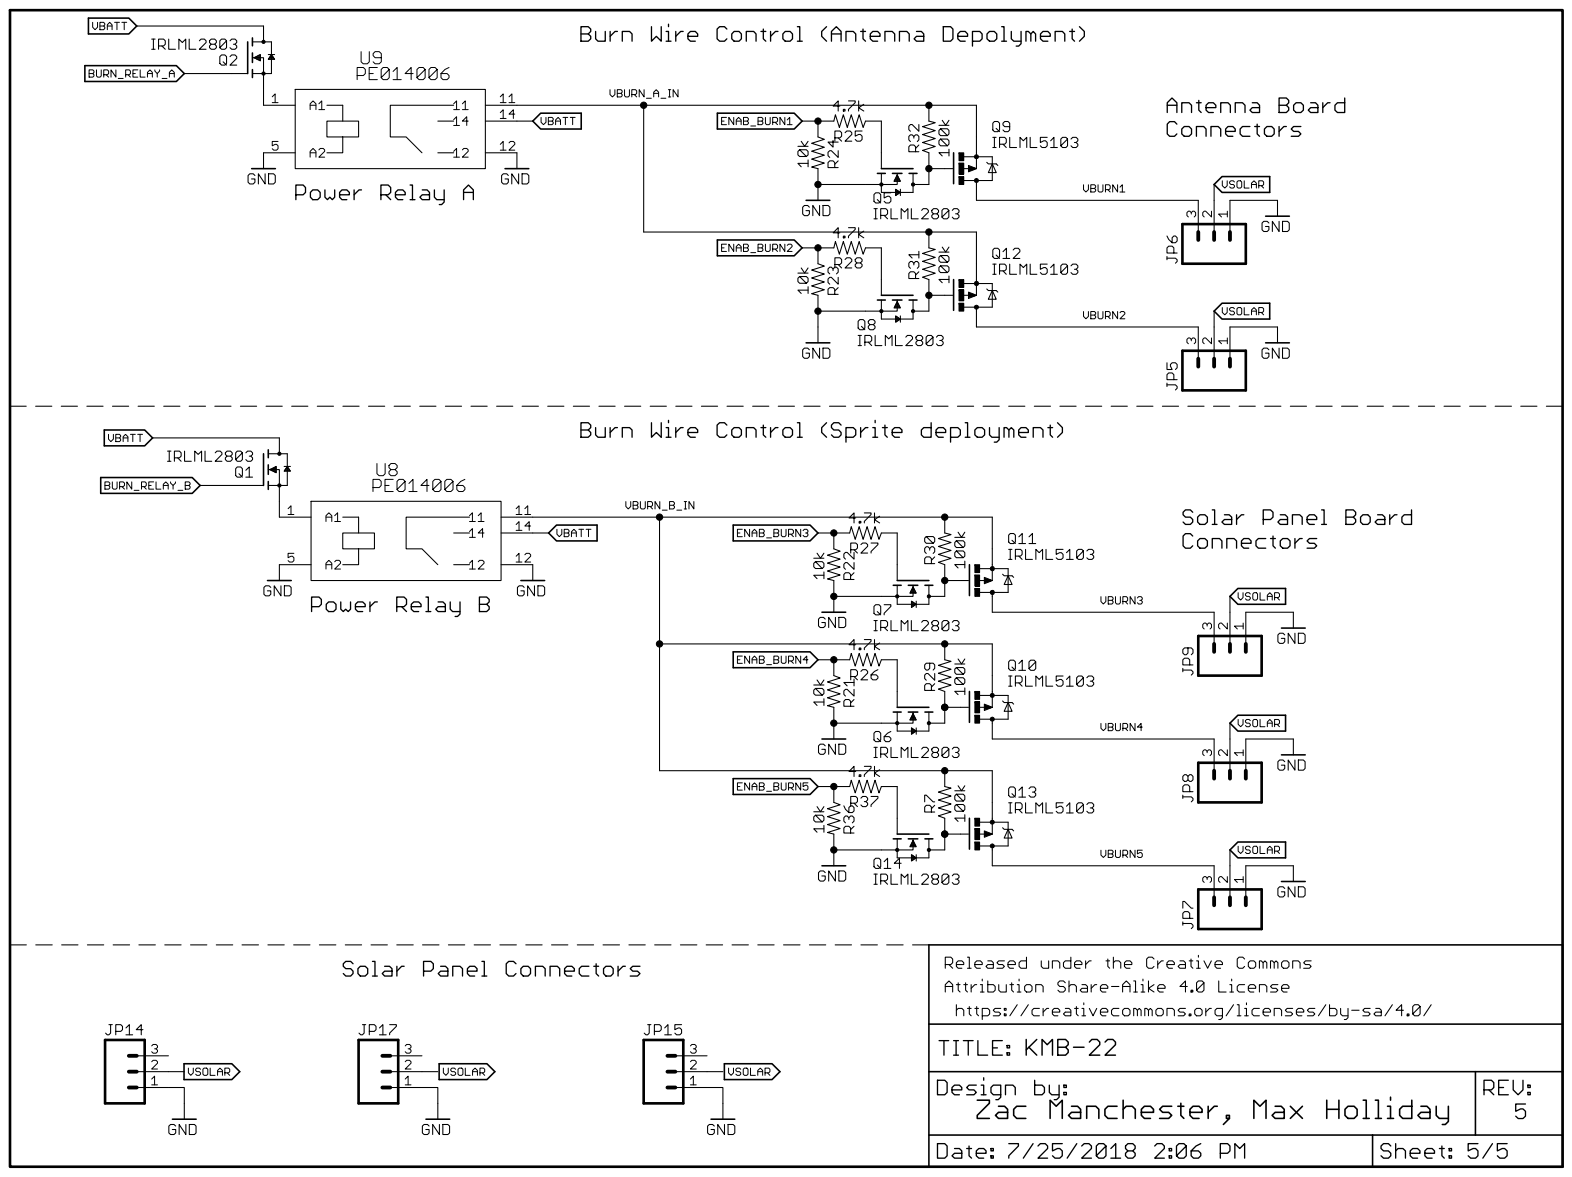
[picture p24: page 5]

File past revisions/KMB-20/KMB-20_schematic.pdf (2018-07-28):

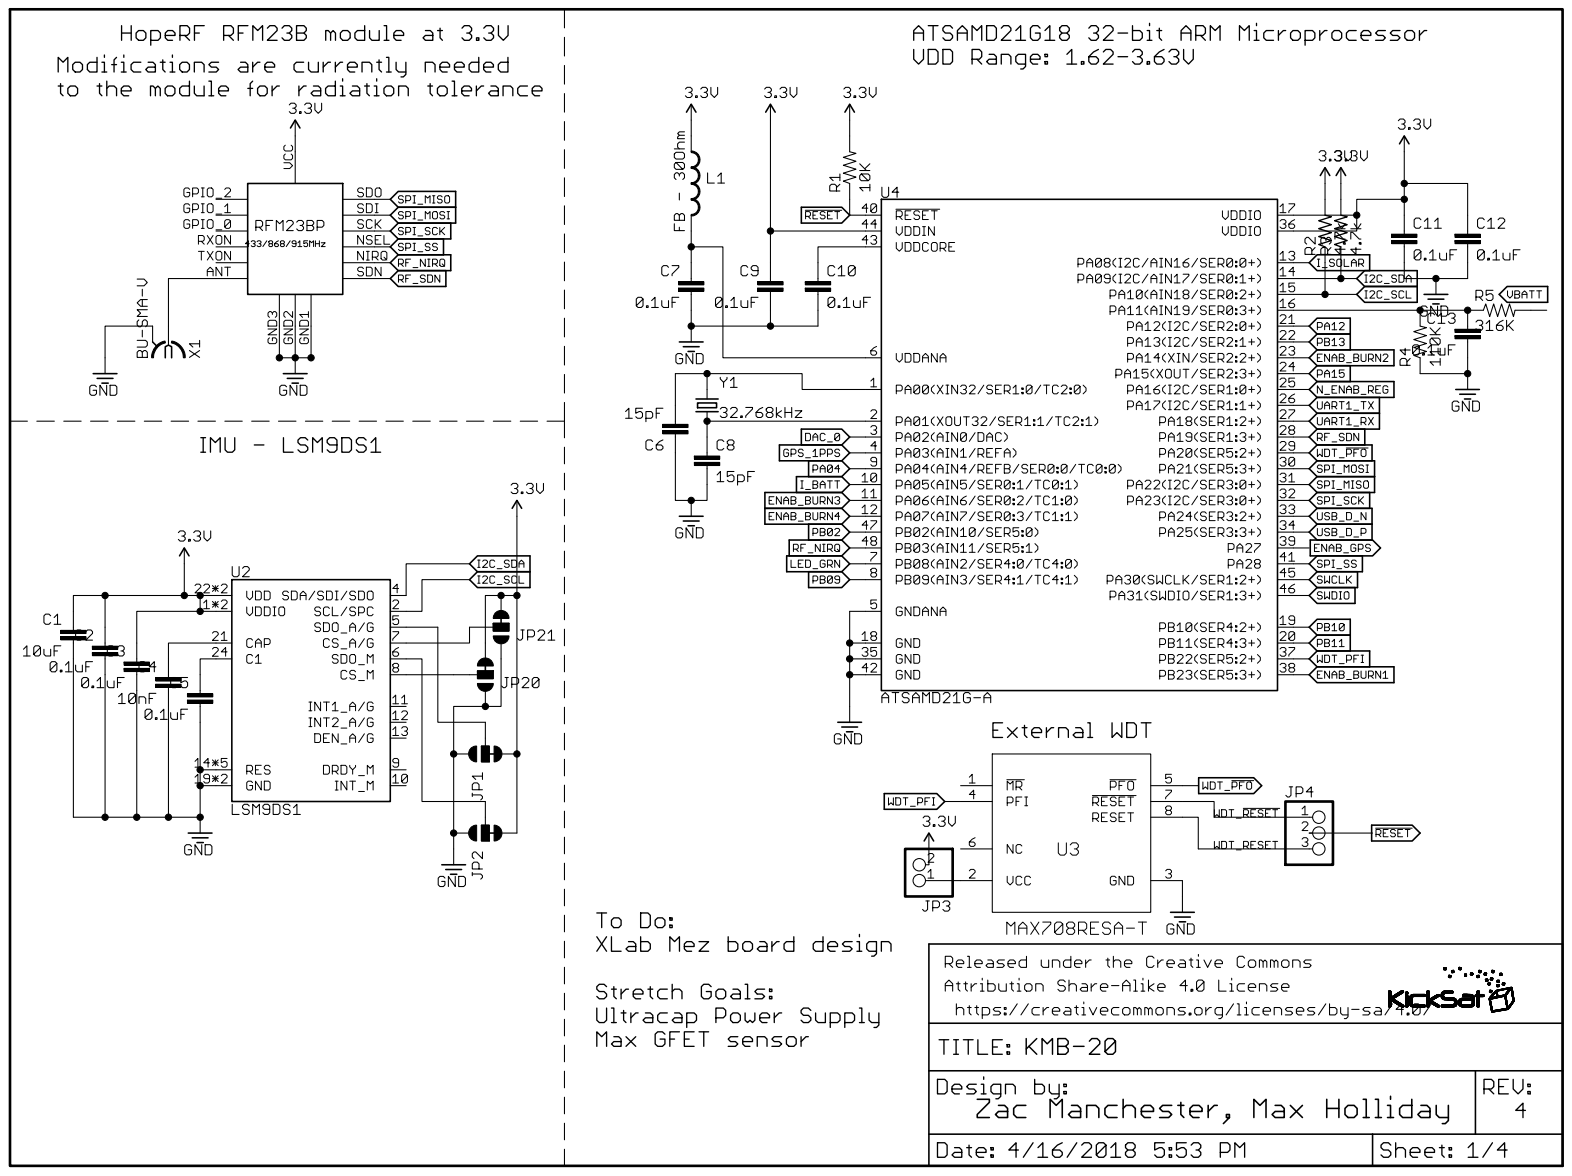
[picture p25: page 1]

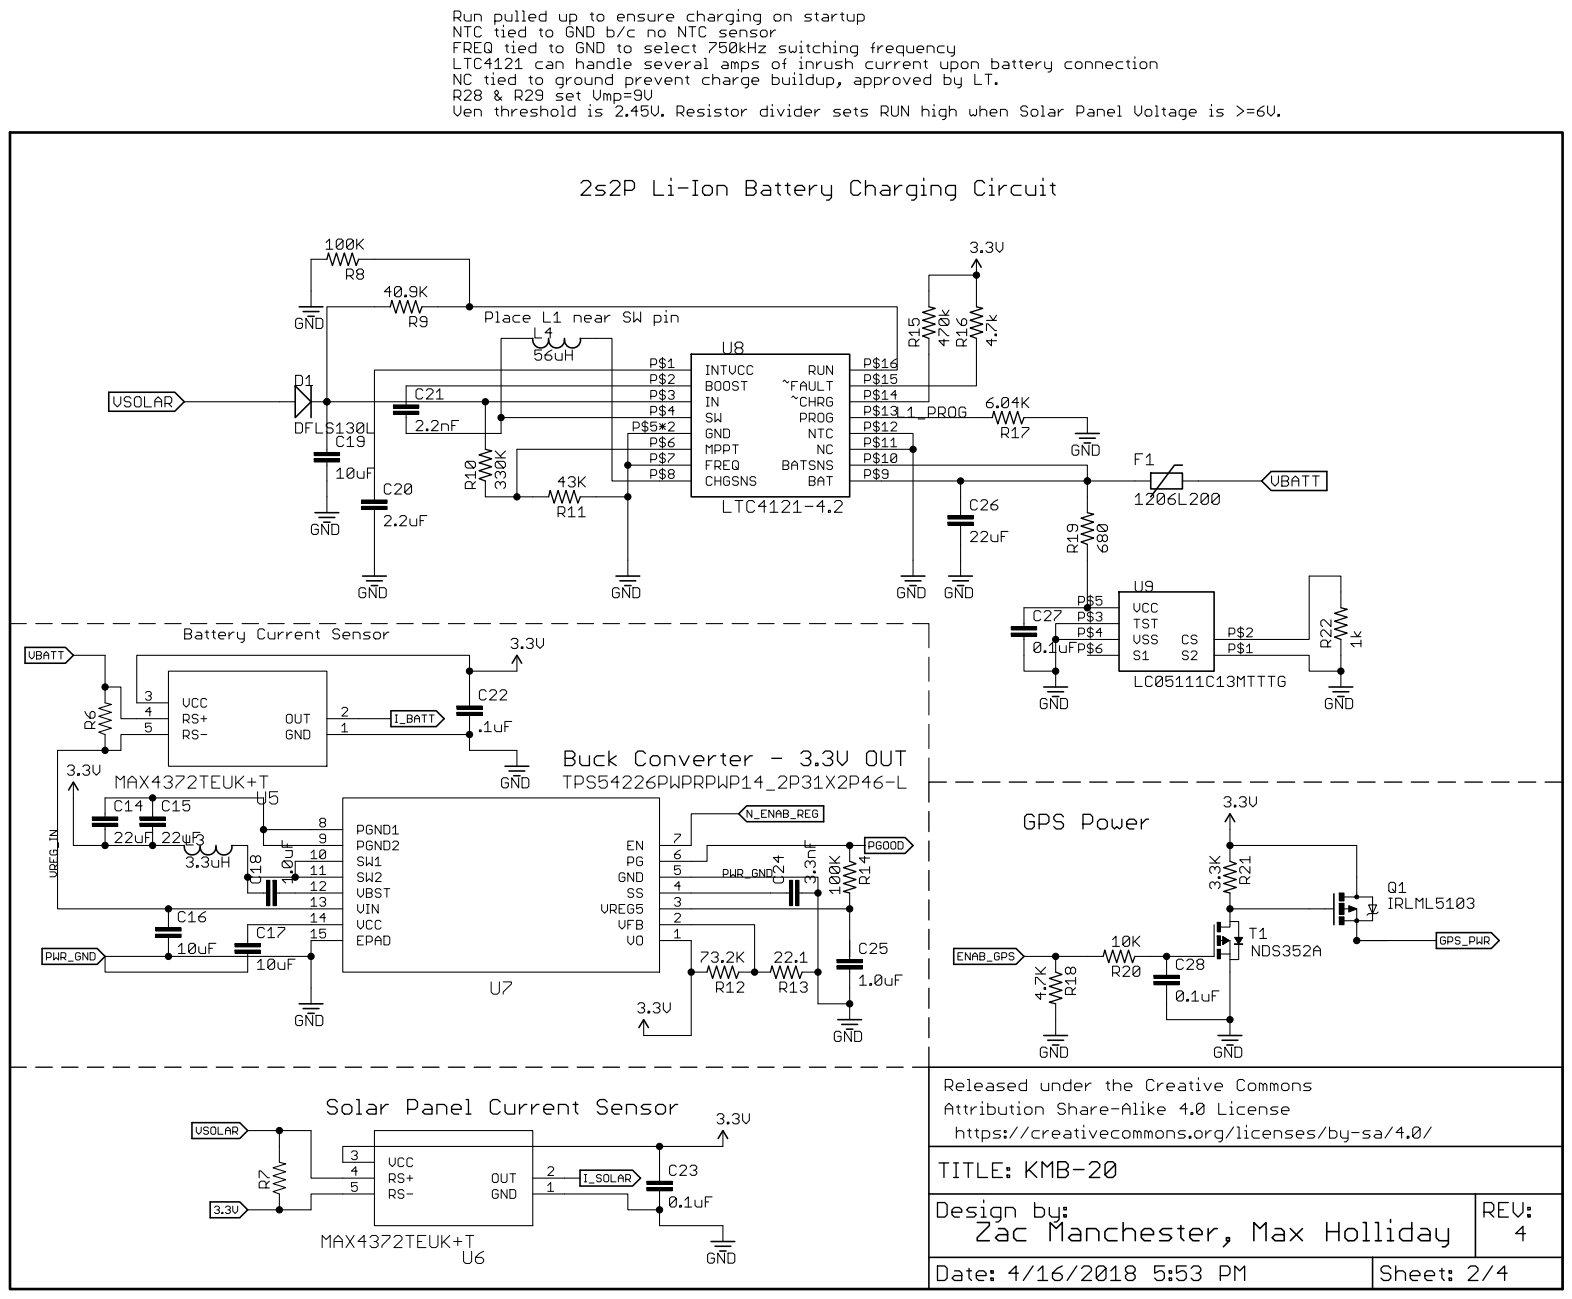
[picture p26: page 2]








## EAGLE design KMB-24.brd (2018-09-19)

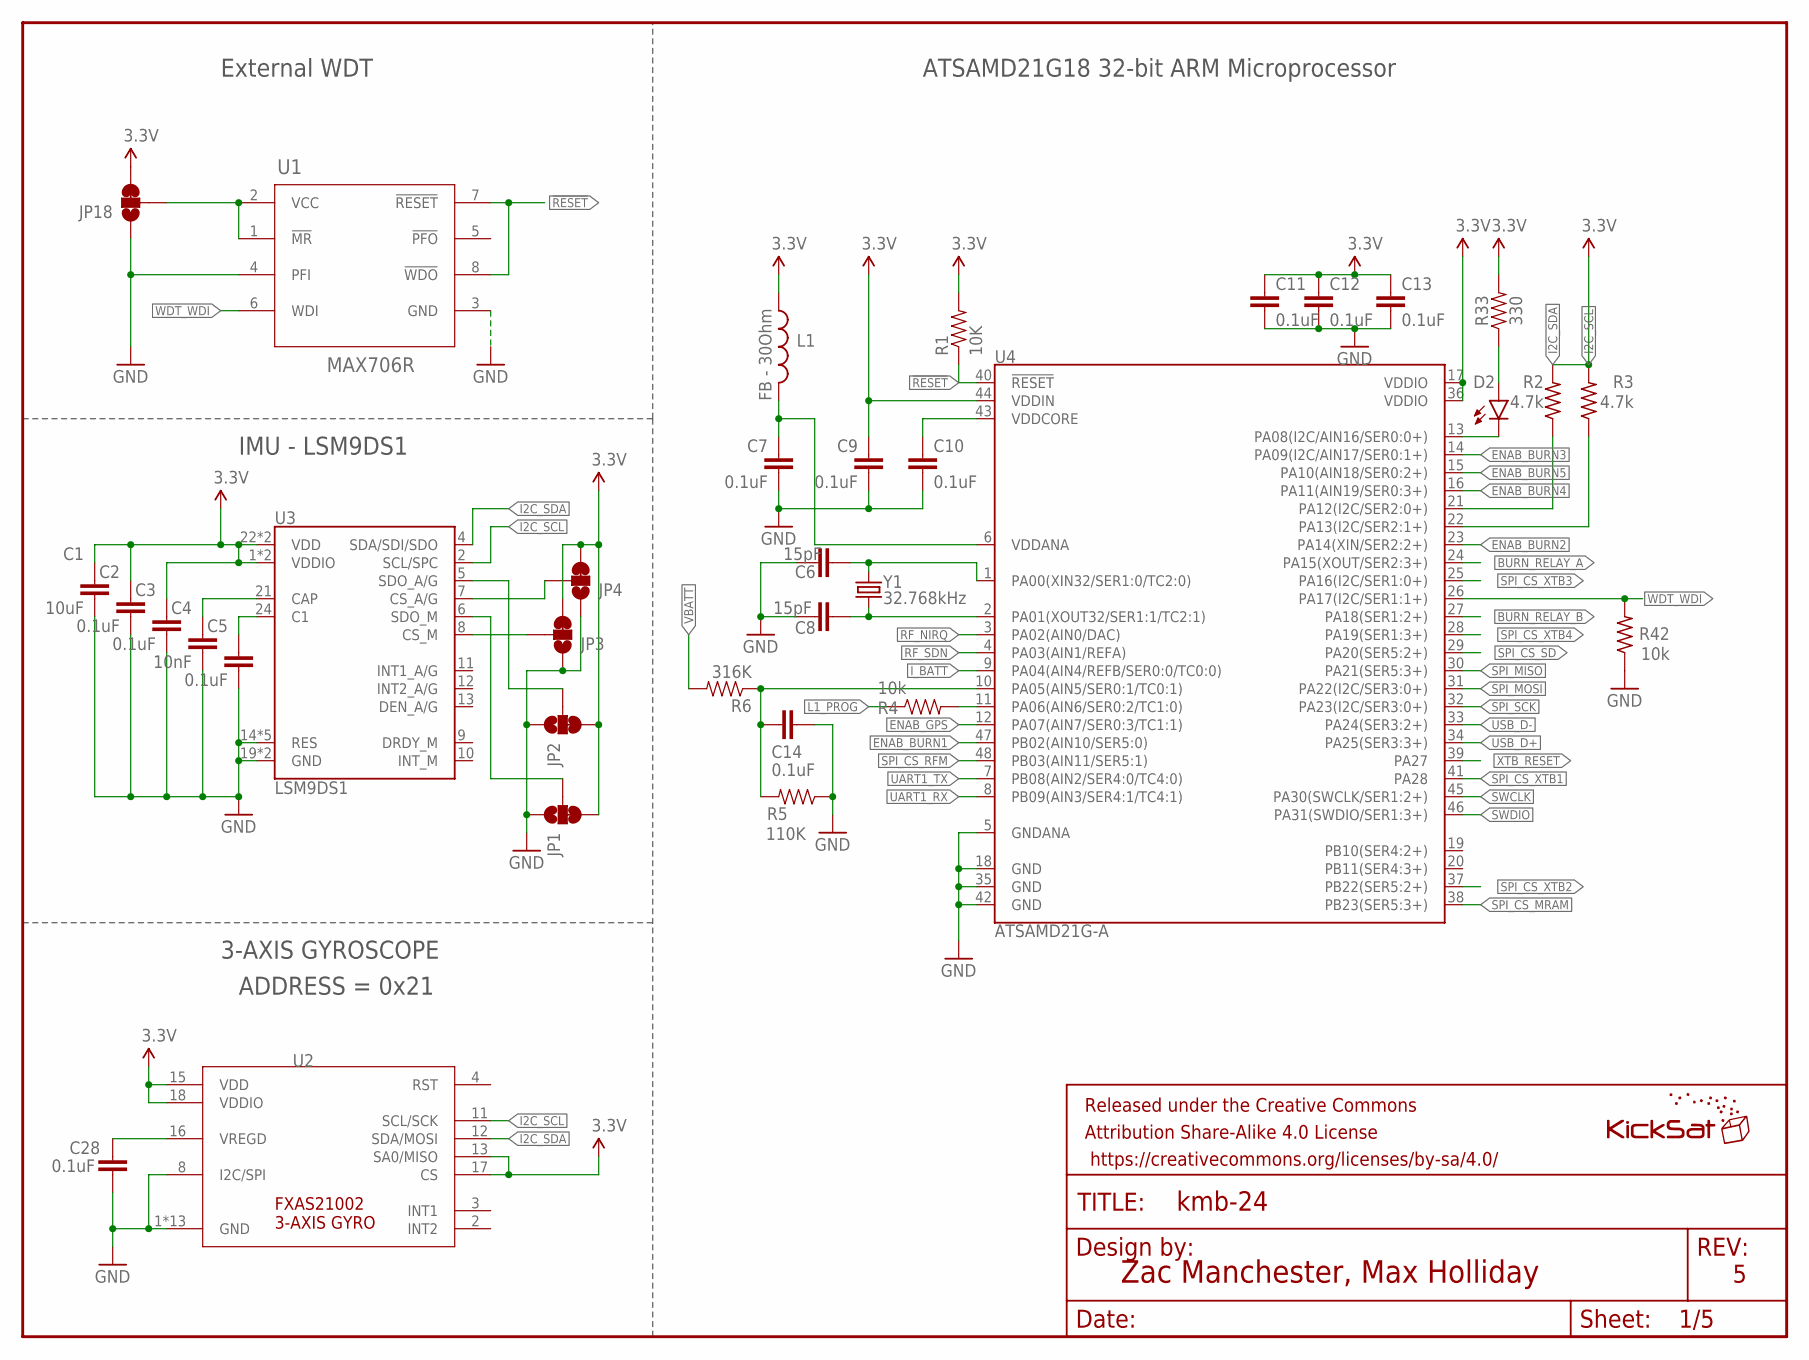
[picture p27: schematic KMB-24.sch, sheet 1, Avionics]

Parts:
C1: 10uF; 0603-CAP
C2, C3, C5, C7, C9, C10, C11, C12, C13, C14, C28: 0.1uF; 0603-CAP
C4: 10nF; 0603-CAP
C6, C8: 15pF; 0603-CAP@1
D2: GREEN; LED-0603
FRAME1: FRAME-LETTER; CREATIVE_COMMONS
JP1, JP2, JP3, JP4, JP18: JUMPER-PAD-3-2OF3_NC_BY_TRACE_SMALL; PAD-JUMPER-3-2OF3_NC_BY_TRACE_YES_SILK_FULL_BOX
L1: FB - 30Ohm; 0603
L2: KICKSAT_LOGO
R1: 10K; 0603-RES
R2, R3: 4.7k; R0603
R4: 10k; 0603-RES
R5: 110K; 0603-RES
R6: 316K; 0603-RES
R33: 330; 0603-RES
R42: 10k; R0603
U1: MAX706R; SO8
U2: FXAS21002FXAS21002; QFN50P456X400X100-24
U3: LSM9DS1; LGA24-8X4
U4: ATSAMD21G-A; TQFP-48
Y1: 32.768kHz; CRYSTAL-SMD-3.2X1.5MM

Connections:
3.3V: C1.1, C2.1, C3.1, C9.1, C11.1, C12.1, C13.1, JP1.3, JP2.3, JP3.3, JP4.3, JP18.3, L1.1, R1.2, R2.2, R3.2, R33.2, U2.13 (SA0/MISO), U2.15 (VDD), U2.17 (CS), U2.18 (VDDIO), U3.1 (VDDIO), U3.3 (VDDIO), U3.22 (VDD), U3.23 (VDD), U4.17 (VDDIO), U4.36 (VDDIO), U4.44 (VDDIN); also elsewhere on the board
!RESET: R1.1, U1.7 (!RESET), U1.8 (!WDO), U4.40 (!RESET!); also elsewhere on the board
BURN_RELAY_A: U4.24 (PA15(XOUT/SER2:3+)); also elsewhere on the board
BURN_RELAY_B: U4.27 (PA18(SER1:2+)); also elsewhere on the board
ENAB_BURN1: U4.47 (PB02(AIN10/SER5:0)); also elsewhere on the board
ENAB_BURN2: U4.23 (PA14(XIN/SER2:2+)); also elsewhere on the board
ENAB_BURN3: U4.14 (PA09(I2C/AIN17/SER0:1+)); also elsewhere on the board
ENAB_BURN4: U4.16 (PA11(AIN19/SER0:3+)); also elsewhere on the board
ENAB_BURN5: U4.15 (PA10(AIN18/SER0:2+)); also elsewhere on the board
ENAB_GPS: U4.12 (PA07(AIN7/SER0:3/TC1:1)); also elsewhere on the board
GND: C1.2, C2.2, C3.2, C4.2, C5.2, C6.1, C7.2, C8.2, C9.2, C10.2, C11.2, C12.2, C13.2, C14.2, C28.1, JP1.1, JP2.1, JP3.1, JP4.1, JP18.1, R5.1, R42.1, U1.3 (GND), U1.4 (PFI), U2.1 (GND), U2.5 (GND), U2.6 (GND), U2.7 (GND), U2.8 (I2C/SPI), U2.9 (GND), U2.10 (GND), U2.14 (GND), U2.19 (GND), U2.20 (GND), U2.21 (GND), U2.22 (GND), U2.23 (GND), U2.24 (GND), U3.14 (RES), U3.15 (RES), U3.16 (RES), U3.17 (RES), U3.18 (RES), U3.19 (GND), U3.20 (GND), U4.5 (GNDANA), U4.18 (GND), U4.35 (GND), U4.42 (GND); also elsewhere on the board
I2C_SCL: R3.1, U2.11 (SCL/SCK), U3.2 (SCL/SPC), U4.22 (PA13(I2C/SER2:1+))
I2C_SDA: R2.1, U2.12 (SDA/MOSI), U3.4 (SDA/SDI/SDO), U4.21 (PA12(I2C/SER2:0+))
I2C_SDOA/G: JP2.2, U3.5 (SDO_A/G)
I_BATT: U4.9 (PA04(AIN4/REFB/SER0:0/TC0:0)); also elsewhere on the board
L1_PROG: R4.1; also elsewhere on the board
unnamed: D2.A, R33.1
unnamed: C4.1, U3.21 (CAP)
unnamed: C5.1, U3.24 (C1)
unnamed: JP18.2, U1.1 (!MR), U1.2 (VCC)
unnamed: C14.1, R5.2, R6.1, U4.10 (PA05(AIN5/SER0:1/TC0:1))
unnamed: C7.1, L1.2, U4.6 (VDDANA)
unnamed: JP1.2, U3.6 (SDO_M)
unnamed: C28.2, U2.16 (VREGD)
unnamed: JP3.2, U3.8 (CS_M)
unnamed: JP4.2, U3.7 (CS_A/G)
unnamed: C6.2, U4.1 (PA00(XIN32/SER1:0/TC2:0)), Y1.P$2 (2)
unnamed: C8.1, U4.2 (PA01(XOUT32/SER1:1/TC2:1)), Y1.P$1 (1)
unnamed: R4.2, U4.11 (PA06(AIN6/SER0:2/TC1:0))
unnamed: D2.C, U4.13 (PA08(I2C/AIN16/SER0:0+))
RF_NIRQ: U4.3 (PA02(AIN0/DAC)); also elsewhere on the board
RF_SDN: U4.4 (PA03(AIN1/REFA)); also elsewhere on the board
SPI_CS_MRAM: U4.38 (PB23(SER5:3+)); also elsewhere on the board
SPI_CS_RFM: U4.48 (PB03(AIN11/SER5:1)); also elsewhere on the board
SPI_CS_SD: U4.29 (PA20(SER5:2+)); also elsewhere on the board
SPI_CS_XTB1: U4.41 (PA28); also elsewhere on the board
SPI_CS_XTB2: U4.37 (PB22(SER5:2+)); also elsewhere on the board
SPI_CS_XTB3: U4.25 (PA16(I2C/SER1:0+)); also elsewhere on the board
SPI_CS_XTB4: U4.28 (PA19(SER1:3+)); also elsewhere on the board
SPI_MISO: U4.30 (PA21(SER5:3+)); also elsewhere on the board
SPI_MOSI: U4.31 (PA22(I2C/SER3:0+)); also elsewhere on the board
SPI_SCK: U4.32 (PA23(I2C/SER3:0+)); also elsewhere on the board
SWCLK: U4.45 (PA30(SWCLK/SER1:2+)); also elsewhere on the board
SWDIO: U4.46 (PA31(SWDIO/SER1:3+)); also elsewhere on the board
UART1_RX: U4.8 (PB09(AIN3/SER4:1/TC4:1)); also elsewhere on the board
UART1_TX: U4.7 (PB08(AIN2/SER4:0/TC4:0)); also elsewhere on the board
USB_D+: U4.34 (PA25(SER3:3+)); also elsewhere on the board
USB_D-: U4.33 (PA24(SER3:2+)); also elsewhere on the board
VBATT: R6.2; also elsewhere on the board
VDDCORE3: C10.1, U4.43 (VDDCORE)
WDT_WDI: R42.2, U1.6 (WDI), U4.26 (PA17(I2C/SER1:1+))
XTB_RESET: U4.39 (PA27); also elsewhere on the board

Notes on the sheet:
Zac Manchester, Max Holliday
ATSAMD21G18 32-bit ARM Microprocessor
IMU - LSM9DS1
External WDT
3-AXIS GYROSCOPE
ADDRESS = 0x21

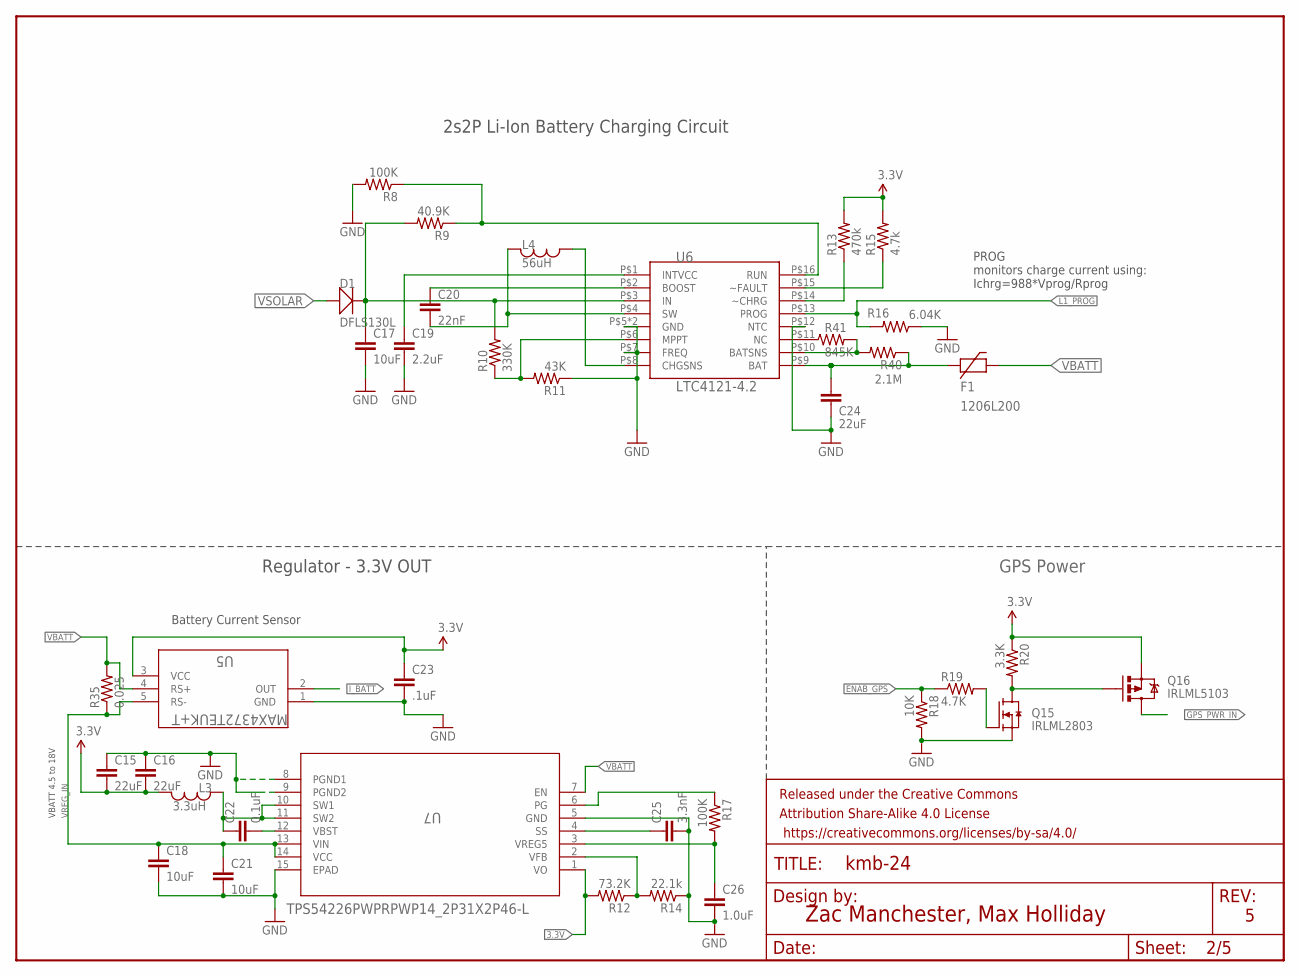
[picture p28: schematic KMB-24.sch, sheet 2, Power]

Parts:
C15, C16: 22uF; 0805
C17, C18, C21: 10uF; 0603
C19: 2.2uF; 0603
C20: 22nF; 0603
C22: 0.1uF; 0603
C23: .1uF; 0603-CAP@1
C24: 22uF; 0603
C25: 3.3nF; 0603
C26: 1.0uF; 0603
D1: DFLS130L; PWRDI-123
F1: 1206L200; 1206
FRAME2: FRAME-LETTER; CREATIVE_COMMONS
L3: 3.3uH; 1812
L4: 56uH; 1812
Q15: IRLML2803; SOT-23
Q16: IRLML5103; SOT23-3
R8, R17: 100K; R0603
R9: 40.9K; R0603
R10: 330K; R0603
R11: 43K; R0603
R12: 73.2K; R0603
R13: 470k; R0603
R14: 22.1k; R0603
R15: 4.7k; R0603
R16: 6.04K; R0603
R18: 10K; R0603
R19: 4.7K; R0603
R20: 3.3K; R0603
R35: 0.025; R2512
R40: 2.1M; R0603
R41: 845K; R0603
U5: MAX4372TEUK+T; 21-0057F
U6: LTC4121-4.2; QFN-16-PAD
U7: TPS54226PWPRPWP14_2P31X2P46-L; PWP14_2P31X2P46-L

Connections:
3.3V: C15.2, C16.2, C23.1, L3.P$1, Q16.2 (S), R12.2, R13.2, R15.2, R20.1, U5.3 (VCC), U7.1 (VO); also elsewhere on the board
ENAB_GPS: R18.1, R19.1; also elsewhere on the board
GND: C15.1, C16.1, C17.2, C18.2, C19.2, C21.2, C23.2, C24.2, C25.2, C26.2, Q15.2 (S), R8.2, R11.1, R14.1, R16.1, R18.2, U5.1 (GND), U6.P$5 (GND), U6.P$7 (FREQ), U6.P$12 (NTC), U6.P$17 (GND), U7.5 (GND), U7.8 (PGND1), U7.9 (PGND2), U7.15 (EPAD); also elsewhere on the board
GPS_PWR_IN: Q16.3 (D); also elsewhere on the board
I_BATT: U5.2 (OUT); also elsewhere on the board
L1_CHG: R8.1, R9.1, U6.P$16 (RUN)
L1_FAULTN: R15.1, U6.P$15 (~FAULT)
L1_PROG: R16.2, U6.P$13 (PROG); also elsewhere on the board
LION1: C24.1, F1.1, R40.1, U6.P$9 (BAT)
unnamed: C22.1, L3.P$2, U7.10 (SW1), U7.11 (SW2)
unnamed: Q15.1 (G), R19.2
unnamed: Q15.3 (D), Q16.1 (G), R20.2
unnamed: C22.2, U7.12 (VBST)
unnamed: R40.2, R41.2, U6.P$10 (BATSNS)
unnamed: C20.2, L4.P$1, U6.P$4 (SW)
unnamed: C20.1, U6.P$2 (BOOST)
unnamed: C19.1, U6.P$1 (INTVCC)
unnamed: R10.1, R11.2, U6.P$6 (MPPT)
unnamed: L4.P$2, U6.P$8 (CHGSNS)
unnamed: R13.1, U6.P$14 (~CHRG)
unnamed: C26.1, R17.2, U7.3 (VREG5)
unnamed: C25.1, U7.4 (SS)
unnamed: R12.1, R14.2, U7.2 (VFB)
unnamed: R41.1, U6.P$11 (NC)
PGOOD: R17.1, U7.6 (PG)
VBATT: F1.2, R35.2, U5.4 (RS+), U7.7 (EN); also elsewhere on the board
VREG_IN: C18.1, C21.1, R35.1, U5.5 (RS-), U7.13 (VIN), U7.14 (VCC)
VSOLAR: D1.A; also elsewhere on the board
VSOLAR_IN: C17.1, D1.C, R9.2, R10.2, U6.P$3 (IN)

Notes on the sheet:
Battery Current Sensor
Zac Manchester, Max Holliday
GPS Power
2s2P Li-Ion Battery Charging Circuit
Regulator - 3.3V OUT
VBATT 4.5 to 18V
PROG monitors charge current using: Ichrg=988*Vprog/Rprog

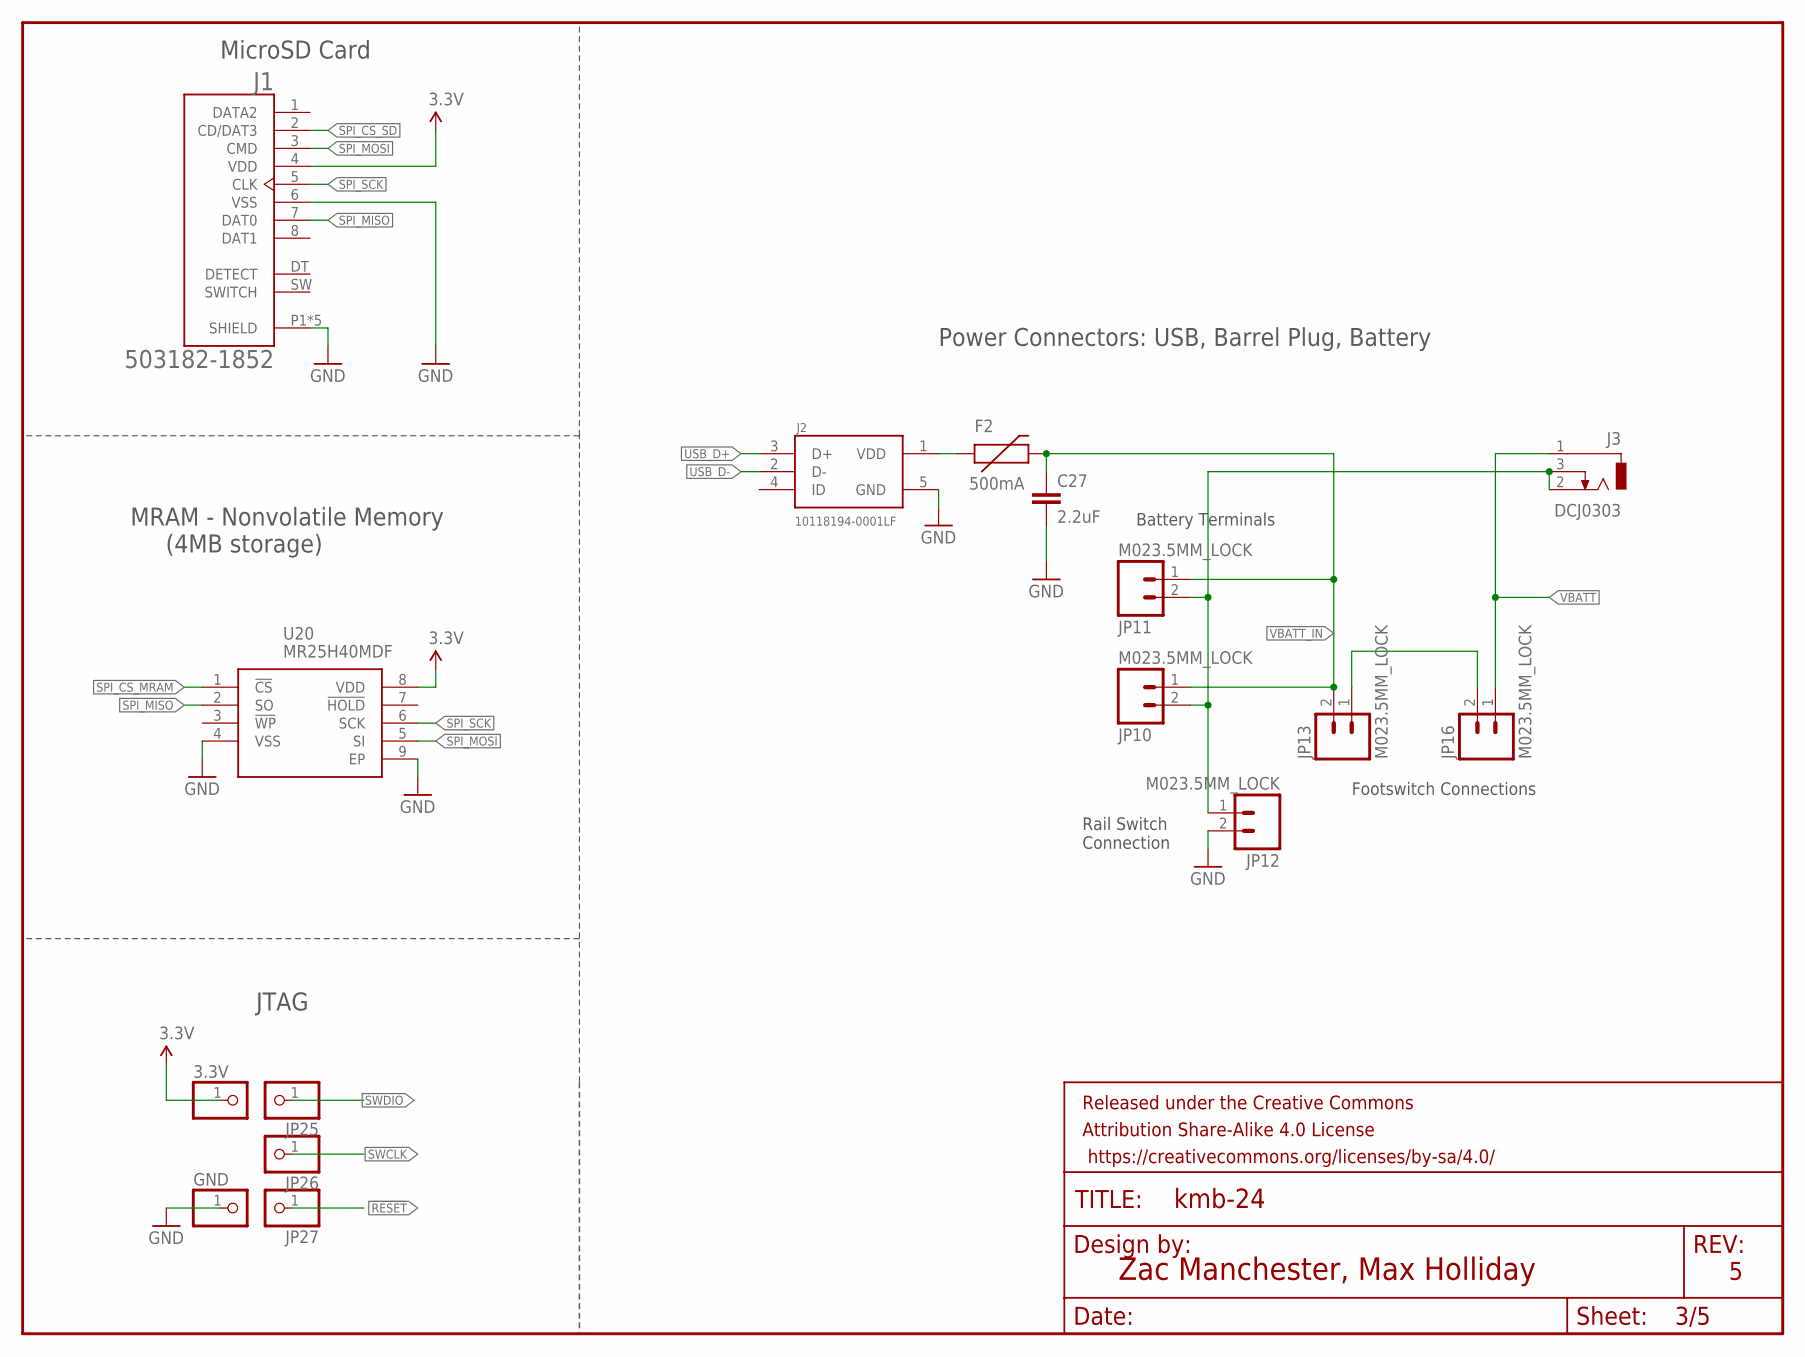
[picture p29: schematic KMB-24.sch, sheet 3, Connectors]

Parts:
3.3V: PINHD-1X1; 1X01
C27: 2.2uF; 0603
F2: 500mA; PTC-1206
FRAME3: FRAME-LETTER; CREATIVE_COMMONS
GND: PINHD-1X1; 1X01
J1: 503182-1852; MOLEX_503182-1852
J2: 10118194-0001LF; FRAMATOME_10118194-0001LF
J3: DCJ0303
JP10, JP11, JP12, JP13, JP16: M023.5MM_LOCK; SCREWTERMINAL-3.5MM-2_LOCK
JP25, JP26, JP27: PINHD-1X1; 1X01
U20: MR25H40MDF; SON127P600X500X90-9N

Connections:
3.3V: 3.3V.1, J1.4 (VDD), U20.8 (VDD); also elsewhere on the board
!RESET: JP27.1; also elsewhere on the board
GND: C27.2, GND.1, J1.6 (VSS), J1.P1 (SHIELD), J1.P2 (SHIELD), J1.P3 (SHIELD), J1.P4 (SHIELD), J1.P5 (SHIELD), J2.5 (GND), JP12.2, U20.4 (VSS), U20.9 (EP); also elsewhere on the board
unnamed: JP13.1, JP16.2
unnamed: F2.1, J2.1 (VDD)
unnamed: J3.2, J3.3, JP10.2, JP11.2, JP12.1
SPI_CS_MRAM: U20.1 (!CS); also elsewhere on the board
SPI_CS_SD: J1.2 (CD/DAT3); also elsewhere on the board
SPI_MISO: J1.7 (DAT0), U20.2 (SO); also elsewhere on the board
SPI_MOSI: J1.3 (CMD), U20.5 (SI); also elsewhere on the board
SPI_SCK: J1.5 (CLK), U20.6 (SCK); also elsewhere on the board
SWCLK: JP26.1; also elsewhere on the board
SWDIO: JP25.1; also elsewhere on the board
USB_D+: J2.3 (D+); also elsewhere on the board
USB_D-: J2.2 (D-); also elsewhere on the board
VBATT: J3.1, JP16.1; also elsewhere on the board
VBATT_IN: C27.1, F2.2, JP10.1, JP11.1, JP13.2

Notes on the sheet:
Footswitch Connections
Battery Terminals
Rail Switch Connection
Zac Manchester, Max Holliday
JTAG
Power Connectors: USB, Barrel Plug, Battery
MicroSD Card
MRAM - Nonvolatile Memory (4MB storage)

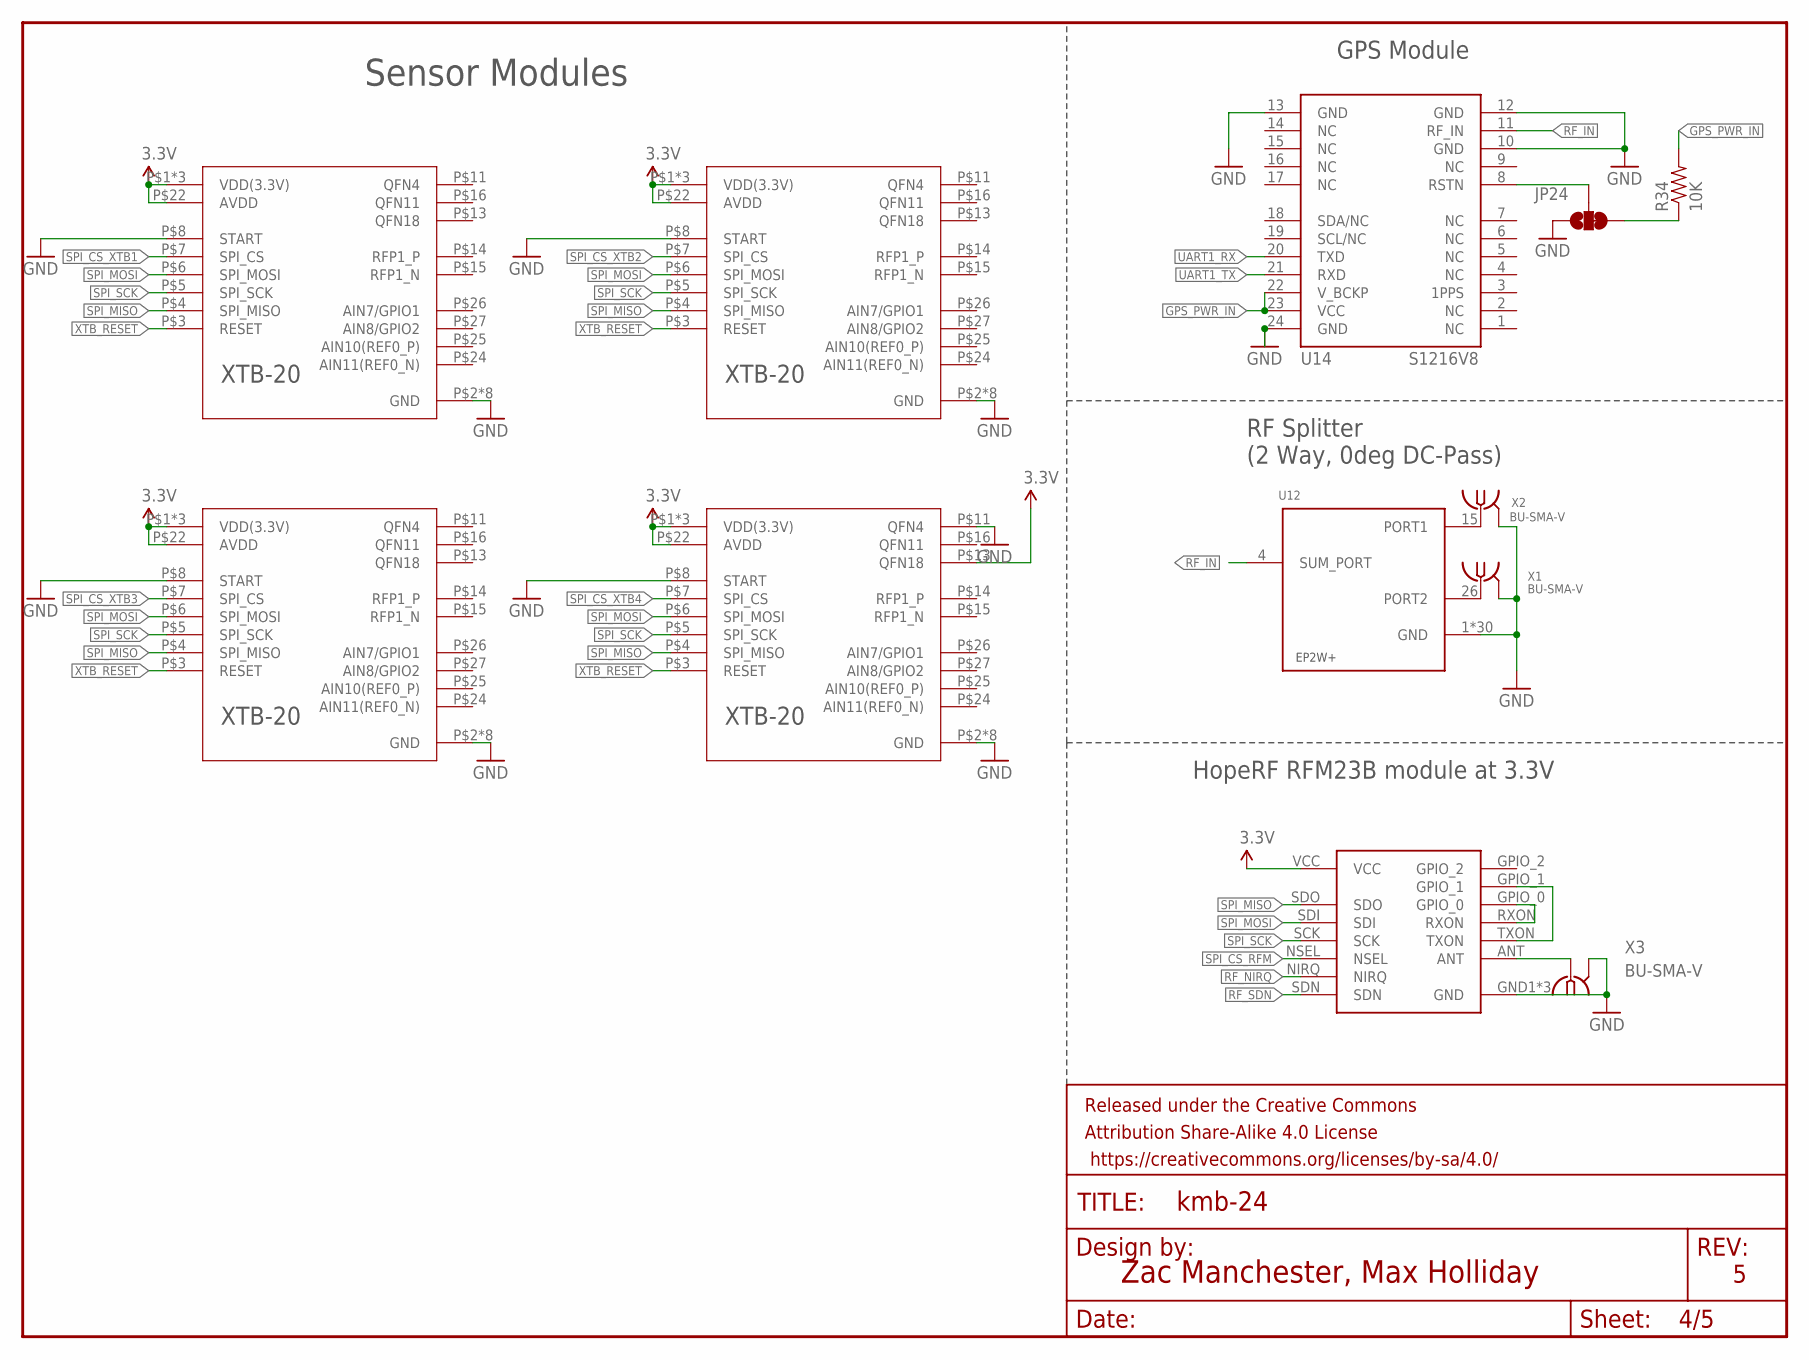
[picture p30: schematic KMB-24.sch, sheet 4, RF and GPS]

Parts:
FRAME4: FRAME-LETTER; CREATIVE_COMMONS
JP24: JUMPER-PAD-3-2OF3_NC_BY_TRACE_SMALL; PAD-JUMPER-3-2OF3_NC_BY_TRACE_YES_SILK_FULL_BOX
R34: 10K; 0603-RES
U12: EP2W+; QFN32-5X5MM
U13: RFM23BP
U14: S1216V8; S1216_24PIN_PACKAGE
U15, U16, U17, U18: XTB_2018_07_15; XTB28_MEZ
X1, X2, X3: BU-SMA-V

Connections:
3.3V: U13.VCC, U15.P$1 (VDD(3.3V)), U15.P$20 (VDD(3.3V)), U15.P$22 (AVDD), U15.P$28 (VDD(3.3V)), U16.P$1 (VDD(3.3V)), U16.P$20 (VDD(3.3V)), U16.P$22 (AVDD), U16.P$28 (VDD(3.3V)), U17.P$1 (VDD(3.3V)), U17.P$20 (VDD(3.3V)), U17.P$22 (AVDD), U17.P$28 (VDD(3.3V)), U18.P$1 (VDD(3.3V)), U18.P$13 (QFN18), U18.P$20 (VDD(3.3V)), U18.P$22 (AVDD), U18.P$28 (VDD(3.3V)); also elsewhere on the board
GND: JP24.1, U12.1 (GND), U12.2 (GND), U12.3 (GND), U12.5 (GND), U12.6 (GND), U12.7 (GND), U12.8 (GND), U12.9 (GND), U12.10 (GND), U12.11 (GND), U12.12 (GND), U12.13 (GND), U12.14 (GND), U12.16 (GND), U12.17 (GND), U12.18 (GND), U12.19 (GND), U12.20 (GND), U12.21 (GND), U12.22 (GND), U12.23 (GND), U12.24 (GND), U12.25 (GND), U12.27 (GND), U12.28 (GND), U12.29 (GND), U12.30 (GND), U12.31 (GND), U12.32 (GND), U12.EP (GND), U13.GND1 (GND), U13.GND2 (GND), U13.GND3 (GND), U14.10 (GND), U14.12 (GND), U14.13 (GND), U14.24 (GND), U15.P$2 (GND), U15.P$8 (START), U15.P$9 (GND), U15.P$10 (GND), U15.P$12 (GND), U15.P$17 (GND), U15.P$19 (GND), U15.P$21 (GND), U15.P$23 (GND), U16.P$2 (GND), U16.P$8 (START), U16.P$9 (GND), U16.P$10 (GND), U16.P$12 (GND), U16.P$17 (GND), U16.P$19 (GND), U16.P$21 (GND), U16.P$23 (GND), U17.P$2 (GND), U17.P$8 (START), U17.P$9 (GND), U17.P$10 (GND), U17.P$12 (GND), U17.P$17 (GND), U17.P$19 (GND), U17.P$21 (GND), U17.P$23 (GND), U18.P$2 (GND), U18.P$8 (START), U18.P$9 (GND), U18.P$10 (GND), U18.P$11 (QFN4), U18.P$12 (GND), U18.P$17 (GND), U18.P$19 (GND), U18.P$21 (GND), U18.P$23 (GND), X1.2, X1.3 (2), X1.4 (2), X1.5 (2), X2.2, X2.3 (2), X2.4 (2), X2.5 (2), X3.2, X3.3 (2), X3.4 (2), X3.5 (2); also elsewhere on the board
GPS_PWR_IN: R34.2, U14.22 (V_BCKP), U14.23 (VCC); also elsewhere on the board
unnamed: JP24.2, U14.8 (RSTN)
unnamed: U12.15 (PORT1), X2.1
unnamed: U12.26 (PORT2), X1.1
unnamed: U13.ANT, X3.1
unnamed: JP24.3, R34.1
unnamed: U13.GPIO_0, U13.RXON
unnamed: U13.GPIO_1, U13.TXON
RF_IN: U12.4 (SUM_PORT), U14.11 (RF_IN)
RF_NIRQ: U13.NIRQ; also elsewhere on the board
RF_SDN: U13.SDN; also elsewhere on the board
SPI_CS_RFM: U13.NSEL; also elsewhere on the board
SPI_CS_XTB1: U15.P$7 (SPI_CS); also elsewhere on the board
SPI_CS_XTB2: U16.P$7 (SPI_CS); also elsewhere on the board
SPI_CS_XTB3: U17.P$7 (SPI_CS); also elsewhere on the board
SPI_CS_XTB4: U18.P$7 (SPI_CS); also elsewhere on the board
SPI_MISO: U13.SDO, U15.P$4 (SPI_MISO), U16.P$4 (SPI_MISO), U17.P$4 (SPI_MISO), U18.P$4 (SPI_MISO); also elsewhere on the board
SPI_MOSI: U13.SDI, U15.P$6 (SPI_MOSI), U16.P$6 (SPI_MOSI), U17.P$6 (SPI_MOSI), U18.P$6 (SPI_MOSI); also elsewhere on the board
SPI_SCK: U13.SCK, U15.P$5 (SPI_SCK), U16.P$5 (SPI_SCK), U17.P$5 (SPI_SCK), U18.P$5 (SPI_SCK); also elsewhere on the board
UART1_RX: U14.20 (TXD); also elsewhere on the board
UART1_TX: U14.21 (RXD); also elsewhere on the board
XTB_RESET: U15.P$3 (RESET), U16.P$3 (RESET), U17.P$3 (RESET), U18.P$3 (RESET); also elsewhere on the board

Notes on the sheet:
GPS Module
Zac Manchester, Max Holliday
HopeRF RFM23B module at 3.3V
RF Splitter (2 Way, 0deg DC-Pass)
Sensor Modules

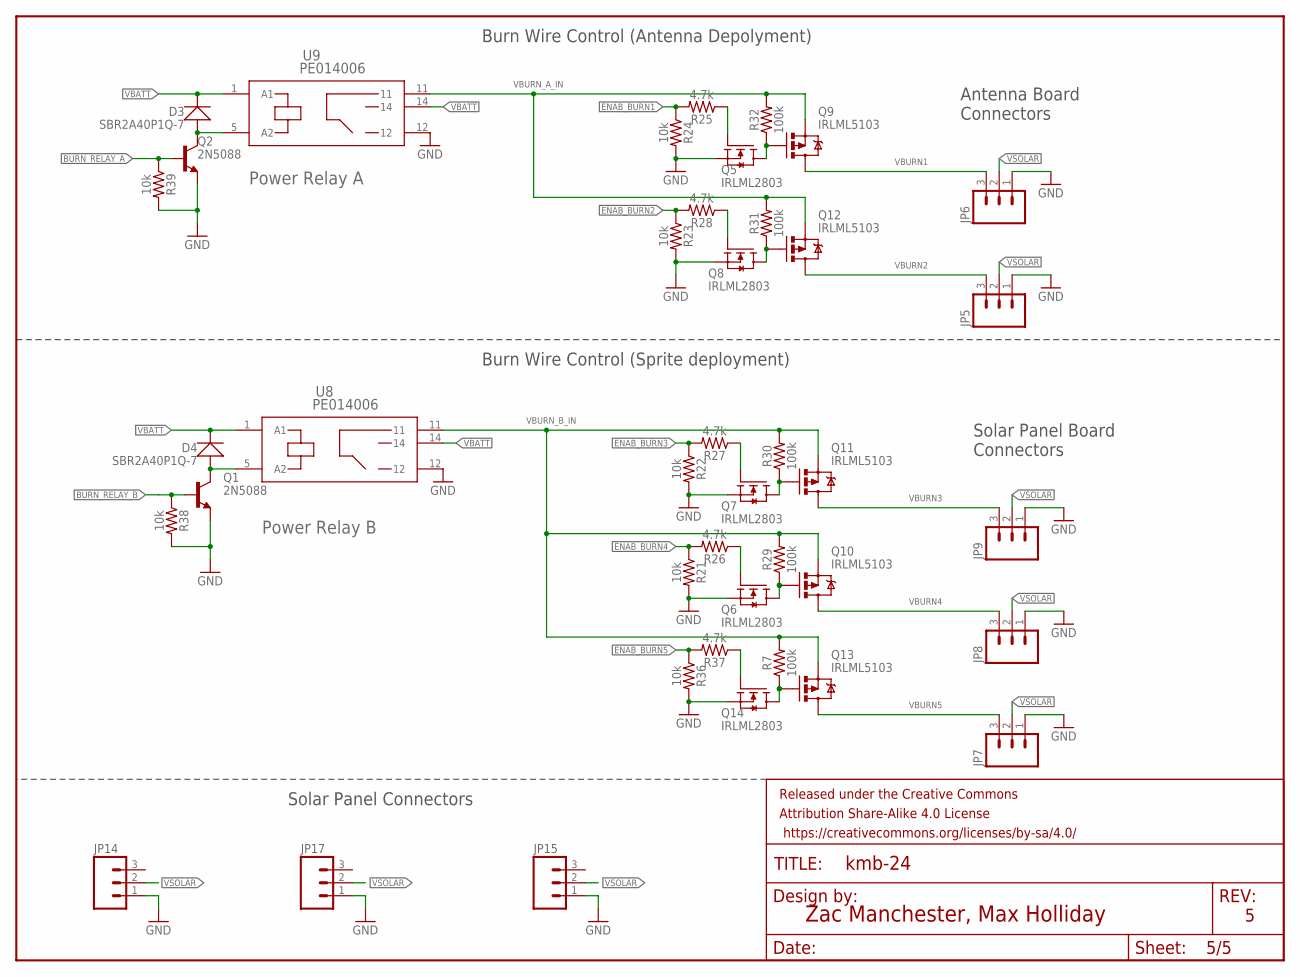
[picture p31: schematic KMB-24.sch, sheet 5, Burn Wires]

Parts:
D3, D4: SBR2A40P1Q-7; PWRDI-123
FRAME5: FRAME-LETTER; CREATIVE_COMMONS
JP5, JP6, JP7, JP8, JP9, JP14, JP15, JP17: M03POLAR_LOCK; MOLEX-1X3_LOCK
Q1, Q2: 2N5088; SOT23
Q5, Q6, Q7, Q8, Q14: IRLML2803; SOT-23
Q9, Q10, Q11, Q12, Q13: IRLML5103; SOT23-3
R7, R29, R30, R31, R32: 100k; 0603
R21, R22, R23, R24, R36, R38, R39: 10k; 0603
R25, R26, R27, R28, R37: 4.7k; 0603
U8, U9: PE014006; RELAY5-PE_CO

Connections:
BURN_RELAY_A: Q2.1 (B), R39.1; also elsewhere on the board
BURN_RELAY_B: Q1.1 (B), R38.1; also elsewhere on the board
ENAB_BURN1: R24.1, R25.2; also elsewhere on the board
ENAB_BURN2: R23.1, R28.2; also elsewhere on the board
ENAB_BURN3: R22.1, R27.2; also elsewhere on the board
ENAB_BURN4: R21.1, R26.2; also elsewhere on the board
ENAB_BURN5: R36.1, R37.2; also elsewhere on the board
GND: JP5.1, JP6.1, JP7.1, JP8.1, JP9.1, JP14.1, JP15.1, JP17.1, Q1.2 (E), Q2.2 (E), Q5.2 (S), Q6.2 (S), Q7.2 (S), Q8.2 (S), Q14.2 (S), R21.2, R22.2, R23.2, R24.2, R36.2, R38.2, R39.2, U8.12, U9.12; also elsewhere on the board
unnamed: Q6.1 (G), R26.1
unnamed: Q5.3 (D), Q9.1 (G), R32.1
unnamed: Q5.1 (G), R25.1
unnamed: Q8.3 (D), Q12.1 (G), R31.1
unnamed: Q8.1 (G), R28.1
unnamed: Q7.1 (G), R27.1
unnamed: D3.A, Q2.3 (C), U9.5 (A2)
unnamed: Q7.3 (D), Q11.1 (G), R30.1
unnamed: Q6.3 (D), Q10.1 (G), R29.1
unnamed: Q13.1 (G), Q14.3 (D), R7.1
unnamed: Q14.1 (G), R37.1
unnamed: D4.A, Q1.3 (C), U8.5 (A2)
VBATT: D3.C, D4.C, U8.1 (A1), U8.14, U9.1 (A1), U9.14; also elsewhere on the board
VBURN1: JP6.3, Q9.3 (D)
VBURN2: JP5.3, Q12.3 (D)
VBURN3: JP9.3, Q11.3 (D)
VBURN4: JP8.3, Q10.3 (D)
VBURN5: JP7.3, Q13.3 (D)
VBURN_A_IN: Q9.2 (S), Q12.2 (S), R31.2, R32.2, U9.11
VBURN_B_IN: Q10.2 (S), Q11.2 (S), Q13.2 (S), R7.2, R29.2, R30.2, U8.11
VSOLAR: JP5.2, JP6.2, JP7.2, JP8.2, JP9.2, JP14.2, JP15.2, JP17.2; also elsewhere on the board

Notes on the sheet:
Zac Manchester, Max Holliday
Power Relay A
Burn Wire Control (Antenna Depolyment)
Burn Wire Control (Sprite deployment)
Power Relay B
Antenna Board Connectors
Solar Panel Board Connectors
Solar Panel Connectors

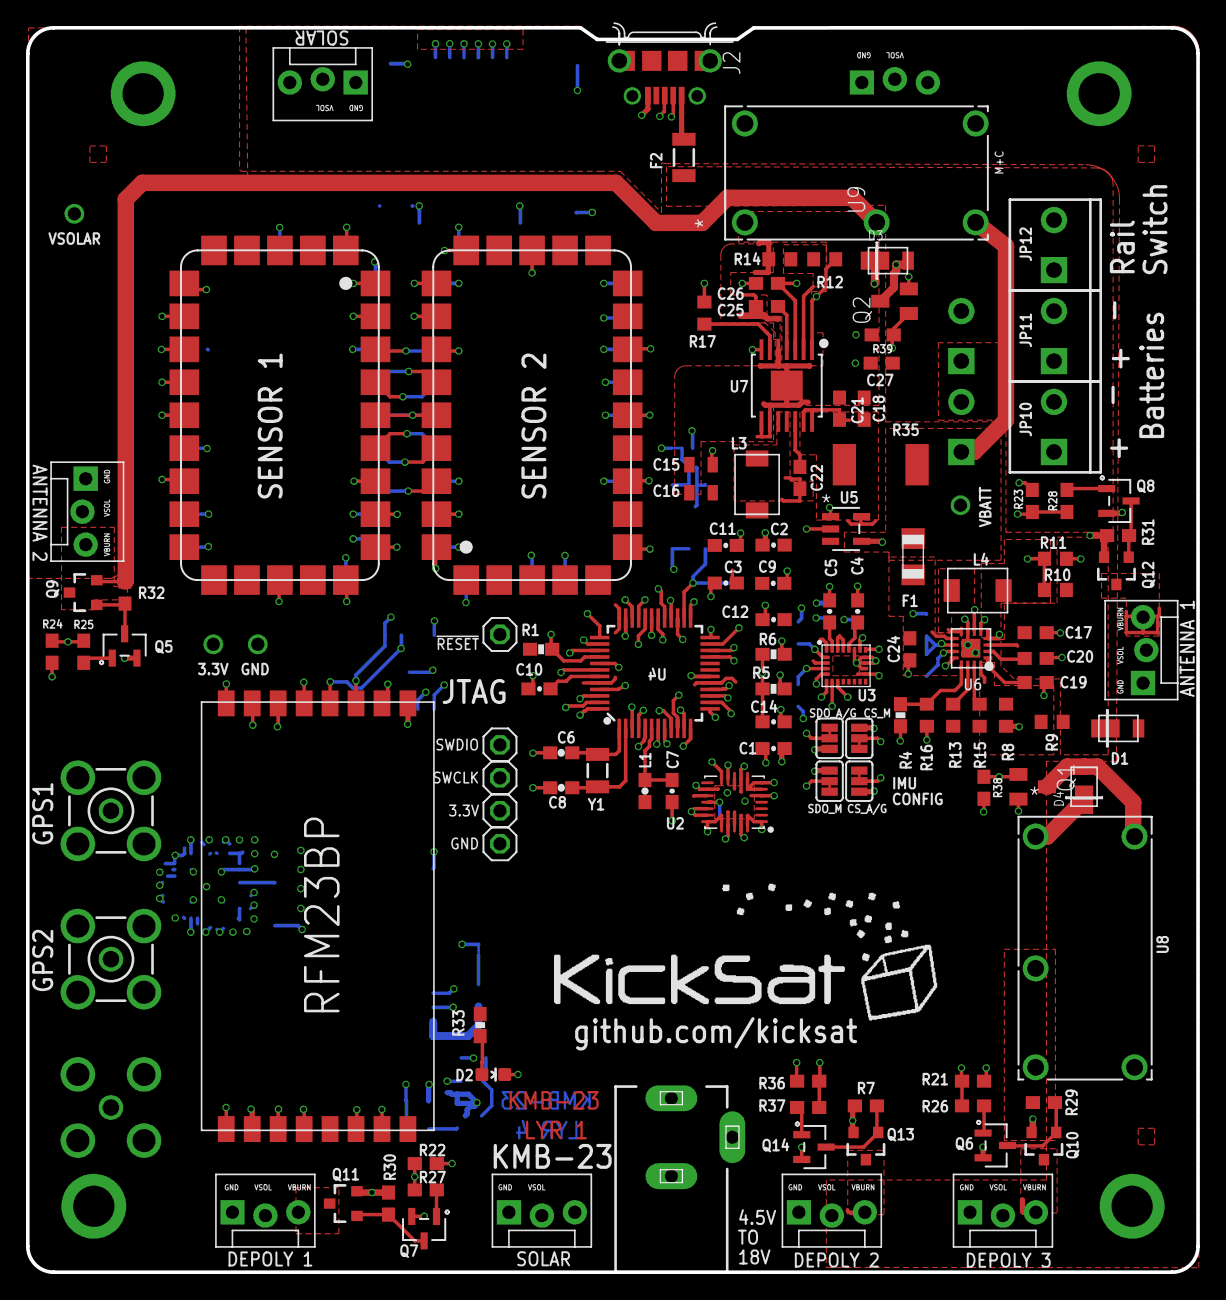
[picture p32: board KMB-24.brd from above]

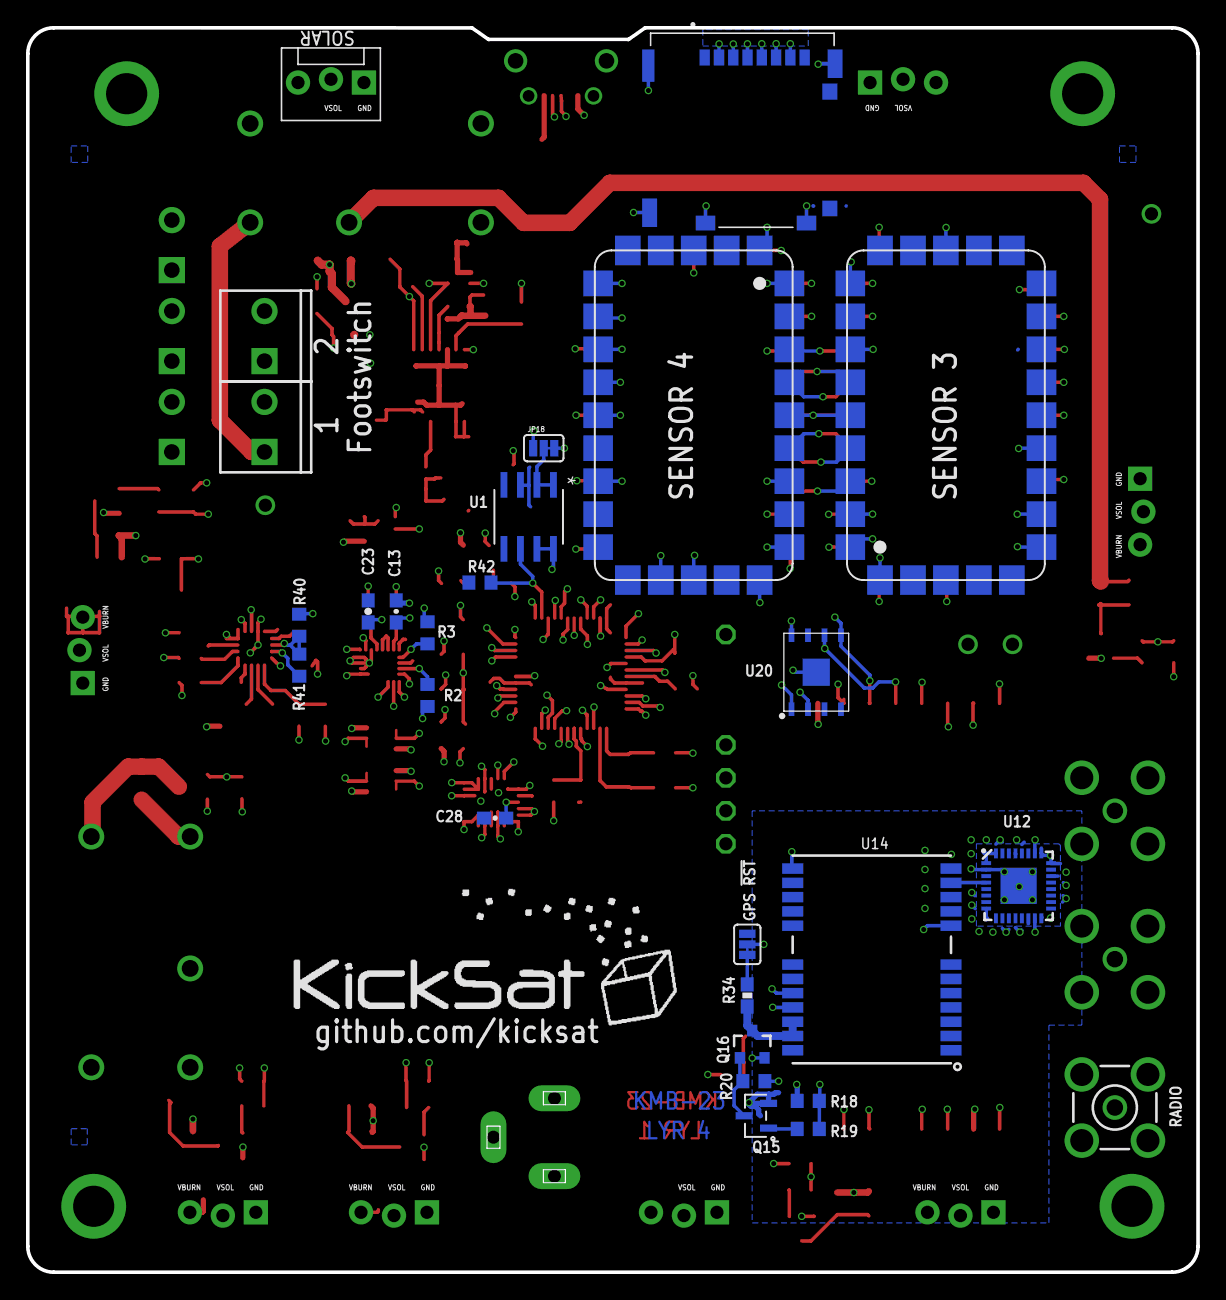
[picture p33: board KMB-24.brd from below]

Board: 4 copper layers, 90.2 x 95.9 mm, 148 parts (28 on the bottom side), 106 nets.

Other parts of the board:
L5: KICKSAT_LOGO

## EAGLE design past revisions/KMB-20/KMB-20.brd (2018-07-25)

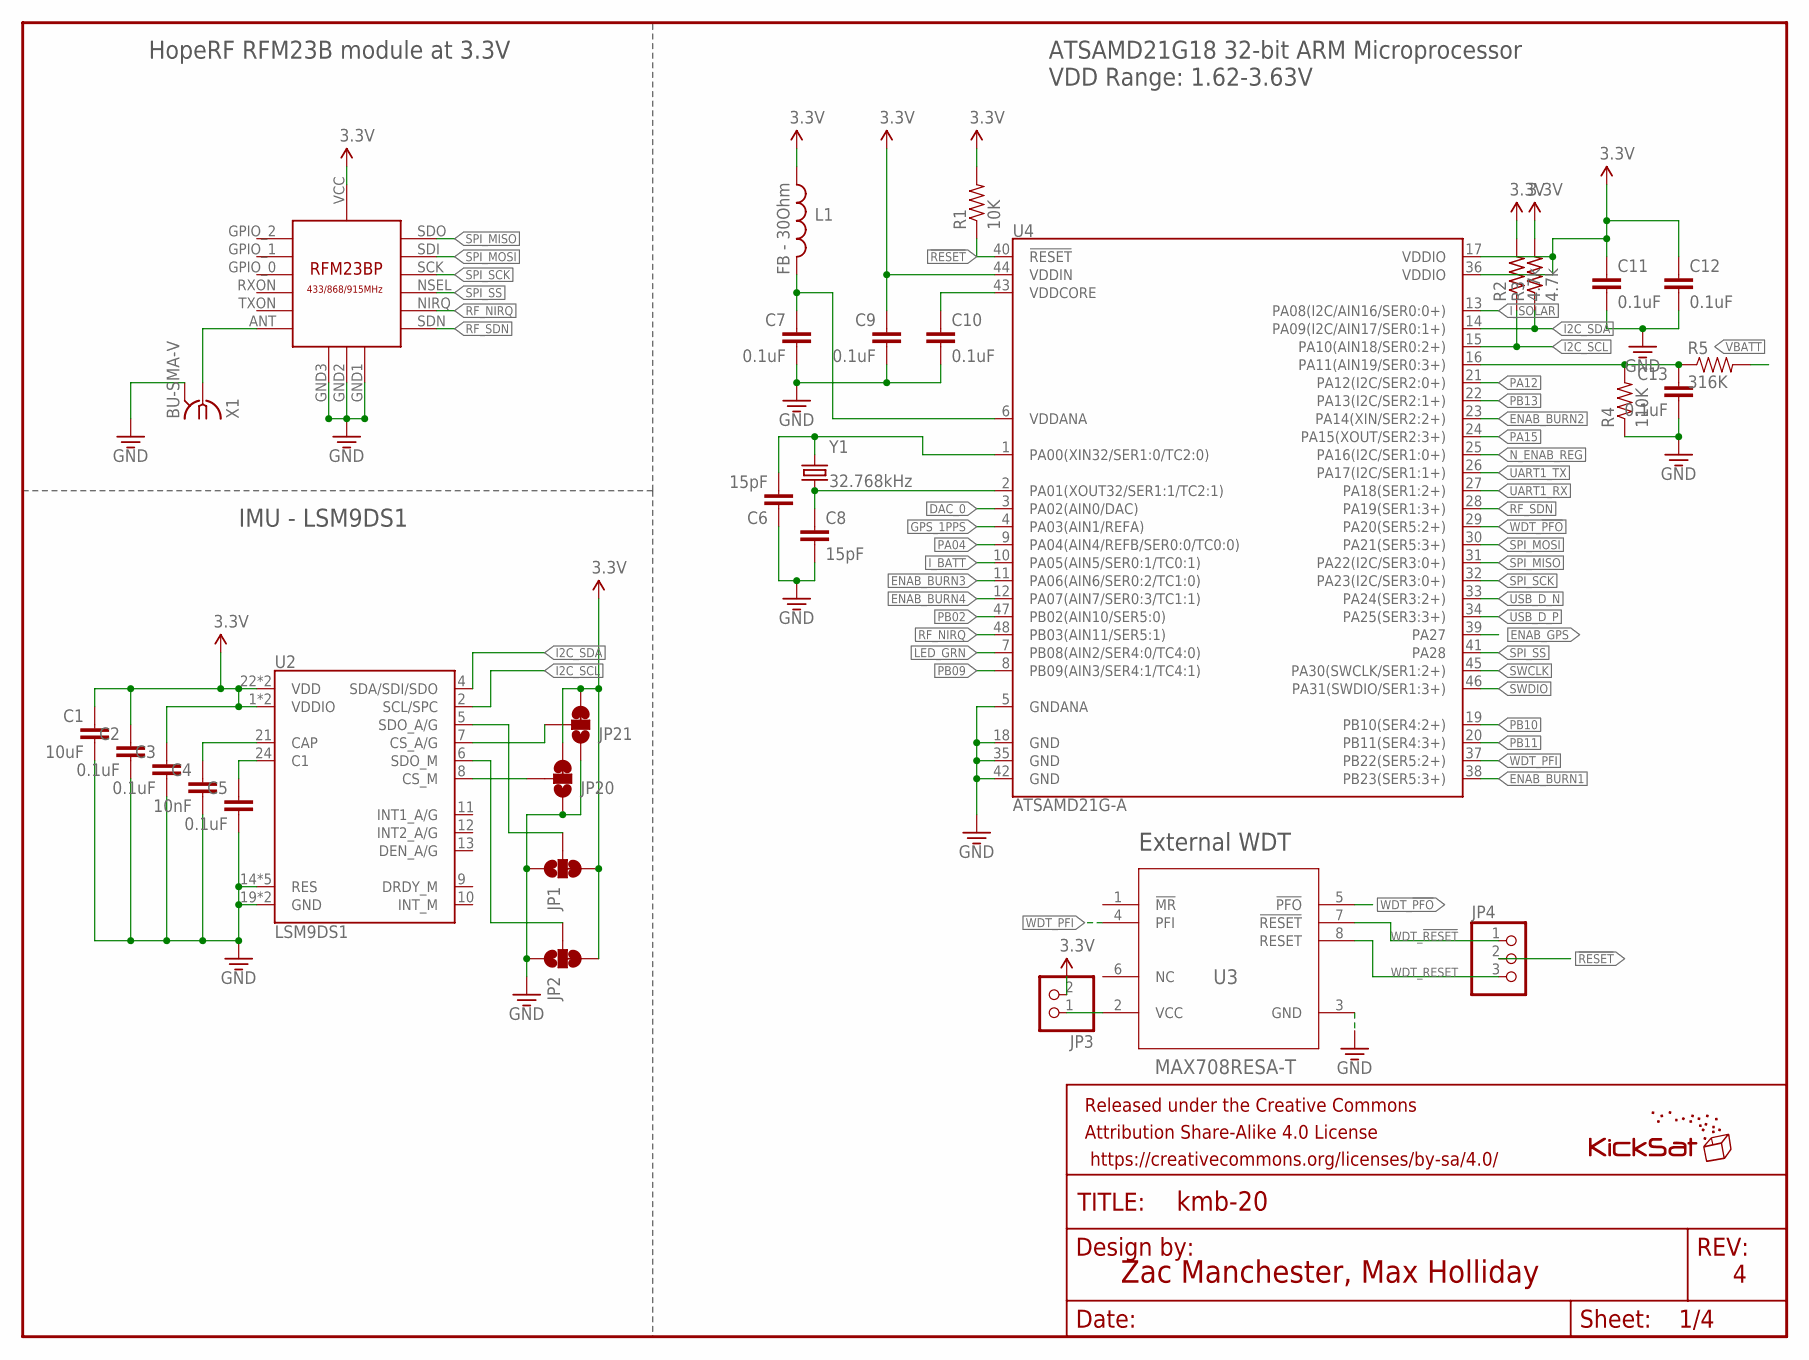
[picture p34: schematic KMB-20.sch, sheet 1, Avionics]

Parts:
C1: 10uF; 0603-CAP
C2, C3, C5, C7, C9, C10, C11, C12, C13: 0.1uF; 0603-CAP
C4: 10nF; 0603-CAP
C6, C8: 15pF; 0603-CAP@1
FRAME1: FRAME-LETTER; CREATIVE_COMMONS
JP1, JP2, JP20, JP21: JUMPER-PAD-3-2OF3_NC_BY_TRACE_SMALL; PAD-JUMPER-3-2OF3_NC_BY_TRACE_YES_SILK_FULL_BOX
JP3: PINHD-1X2; 1X02
JP4: PINHD-1X3; 1X03
L1: FB - 30Ohm; 0603
L2: KICKSAT_LOGO
R1: 10K; 0603-RES
R2, R3: 4.7k; R0603
R4: 110K; 0603-RES
R5: 316K; 0603-RES
U1: RFM23BP
U2: LSM9DS1; LGA24-8X4
U3: MAX708RESA-T; SO8
U4: ATSAMD21G-A; TQFP-48
X1: BU-SMA-V
Y1: 32.768kHz; CRYSTAL-SMD-3.2X1.5MM

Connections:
3.3V: C1.1, C2.1, C3.1, C9.1, C11.1, C12.1, JP1.3, JP2.3, JP3.2, JP20.3, JP21.3, L1.1, R1.2, R2.2, R3.2, U1.VCC, U2.1 (VDDIO), U2.3 (VDDIO), U2.22 (VDD), U2.23 (VDD), U4.17 (VDDIO), U4.36 (VDDIO), U4.44 (VDDIN); also elsewhere on the board
!RESET: JP4.2, R1.1, U4.40 (!RESET!); also elsewhere on the board
DAC_0: U4.3 (PA02(AIN0/DAC)); also elsewhere on the board
ENAB_BURN1: U4.38 (PB23(SER5:3+)); also elsewhere on the board
ENAB_BURN2: U4.23 (PA14(XIN/SER2:2+)); also elsewhere on the board
ENAB_BURN3: U4.11 (PA06(AIN6/SER0:2/TC1:0)); also elsewhere on the board
ENAB_BURN4: U4.12 (PA07(AIN7/SER0:3/TC1:1)); also elsewhere on the board
ENAB_GPS: U4.39 (PA27); also elsewhere on the board
GND: C1.2, C2.2, C3.2, C4.2, C5.2, C6.1, C7.2, C8.2, C9.2, C10.2, C11.2, C12.2, C13.2, JP1.1, JP2.1, JP20.1, JP21.1, R4.1, U1.GND1, U1.GND2, U1.GND3, U2.14 (RES), U2.15 (RES), U2.16 (RES), U2.17 (RES), U2.18 (RES), U2.19 (GND), U2.20 (GND), U3.3 (GND), U4.5 (GNDANA), U4.18 (GND), U4.35 (GND), U4.42 (GND), X1.2, X1.3 (2), X1.4 (2), X1.5 (2); also elsewhere on the board
GPS_1PPS: U4.4 (PA03(AIN1/REFA)); also elsewhere on the board
I2C_SCL: R2.1, U2.2 (SCL/SPC), U4.15 (PA10(AIN18/SER0:2+)); also elsewhere on the board
I2C_SDA: R3.1, U2.4 (SDA/SDI/SDO), U4.14 (PA09(I2C/AIN17/SER0:1+)); also elsewhere on the board
I2C_SDOA/G: JP1.2, U2.5 (SDO_A/G)
I_BATT: U4.10 (PA05(AIN5/SER0:1/TC0:1)); also elsewhere on the board
I_SOLAR: U4.13 (PA08(I2C/AIN16/SER0:0+)); also elsewhere on the board
LED_GRN: U4.7 (PB08(AIN2/SER4:0/TC4:0)); also elsewhere on the board
unnamed: C4.1, U2.21 (CAP)
unnamed: C5.1, U2.24 (C1)
unnamed: JP3.1, U3.2 (VCC)
unnamed: C7.1, L1.2, U4.6 (VDDANA)
unnamed: U1.ANT, X1.1
unnamed: JP2.2, U2.6 (SDO_M)
unnamed: JP20.2, U2.8 (CS_M)
unnamed: JP21.2, U2.7 (CS_A/G)
unnamed: C6.2, U4.1 (PA00(XIN32/SER1:0/TC2:0)), Y1.P$2 (2)
unnamed: C8.1, U4.2 (PA01(XOUT32/SER1:1/TC2:1)), Y1.P$1 (1)
unnamed: C13.1, R4.2, R5.1, U4.16 (PA11(AIN19/SER0:3+))
N_ENAB_REG: U4.25 (PA16(I2C/SER1:0+)); also elsewhere on the board
PA04: U4.9 (PA04(AIN4/REFB/SER0:0/TC0:0))
PA12: U4.21 (PA12(I2C/SER2:0+)); also elsewhere on the board
PA15: U4.24 (PA15(XOUT/SER2:3+))
PB02: U4.47 (PB02(AIN10/SER5:0)); also elsewhere on the board
PB09: U4.8 (PB09(AIN3/SER4:1/TC4:1)); also elsewhere on the board
PB10: U4.19 (PB10(SER4:2+)); also elsewhere on the board
PB11: U4.20 (PB11(SER4:3+)); also elsewhere on the board
PB13: U4.22 (PA13(I2C/SER2:1+))
RF_NIRQ: U1.NIRQ, U4.48 (PB03(AIN11/SER5:1))
RF_SDN: U1.SDN, U4.28 (PA19(SER1:3+))
SPI_MISO: U1.SDO, U4.31 (PA22(I2C/SER3:0+))
SPI_MOSI: U1.SDI, U4.30 (PA21(SER5:3+))
SPI_SCK: U1.SCK, U4.32 (PA23(I2C/SER3:0+))
SPI_SS: U1.NSEL, U4.41 (PA28)
SWCLK: U4.45 (PA30(SWCLK/SER1:2+)); also elsewhere on the board
SWDIO: U4.46 (PA31(SWDIO/SER1:3+)); also elsewhere on the board
UART1_RX: U4.27 (PA18(SER1:2+)); also elsewhere on the board
UART1_TX: U4.26 (PA17(I2C/SER1:1+)); also elsewhere on the board
USB_D_N: U4.33 (PA24(SER3:2+)); also elsewhere on the board
USB_D_P: U4.34 (PA25(SER3:3+)); also elsewhere on the board
VBATT: R5.2; also elsewhere on the board
VDDCORE3: C10.1, U4.43 (VDDCORE)
WDT_!PFO: U3.5 (!PFO), U4.29 (PA20(SER5:2+))
WDT_!RESET: JP4.1, U3.7 (!RESET)
WDT_PFI: U3.4 (PFI), U4.37 (PB22(SER5:2+))
WDT_RESET: JP4.3, U3.8 (RESET)

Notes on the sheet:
Zac Manchester, Max Holliday
ATSAMD21G18 32-bit ARM Microprocessor VDD Range: 1.62-3.63V
HopeRF RFM23B module at 3.3V
IMU - LSM9DS1
External WDT

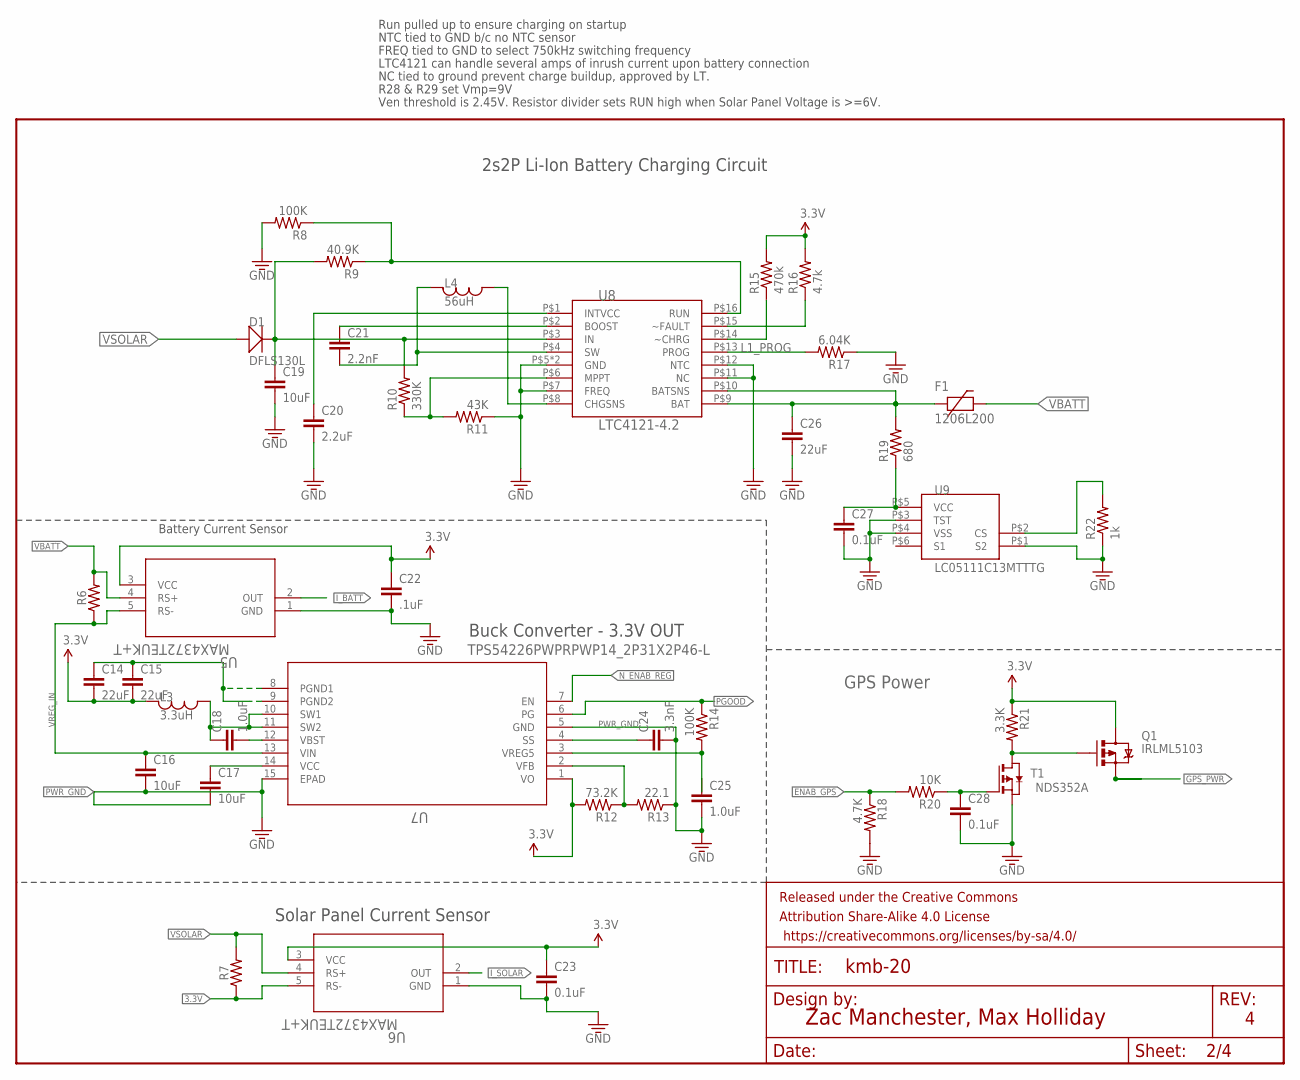
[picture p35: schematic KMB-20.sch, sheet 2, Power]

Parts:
C14, C15: 22uF; 0805
C16, C17, C19: 10uF; 0603
C18, C25: 1.0uF; 0603
C20: 2.2uF; 0603
C21: 2.2nF; 0603
C22: .1uF; 0603-CAP@1
C23, C27, C28: 0.1uF; 0603
C24: 3.3nF; 0603
C26: 22uF; 0603
D1: DFLS130L; PWRDI-123
F1: 1206L200; 1206
FRAME2: FRAME-LETTER; CREATIVE_COMMONS
L3: 3.3uH; 1812
L4: 56uH; 1812
Q1: IRLML5103; SOT23-3
R6, R7: 0603
R8, R14: 100K; R0603
R9: 40.9K; R0603
R10: 330K; R0603
R11: 43K; R0603
R12: 73.2K; R0603
R13: 22.1; R0603
R15: 470k; R0603
R16: 4.7k; R0603
R17: 6.04K; R0603
R18: 4.7K; R0603
R19: 680; R0603
R20: 10K; R0603
R21: 3.3K; R0603
R22: 1k; R0603
T1: NDS352A; SOT-23
U5, U6: MAX4372TEUK+T; 21-0057F
U7: TPS54226PWPRPWP14_2P31X2P46-L; PWP14_2P31X2P46-L
U8: LTC4121-4.2; QFN-16-PAD
U9: LC05111C13MTTTG; WDFN6

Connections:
3.3V: C14.2, C15.2, C22.1, C23.1, L3.P$1, Q1.3 (D), R7.1, R12.2, R15.2, R16.2, R21.1, U5.3 (VCC), U6.3 (VCC), U6.5 (RS-), U7.1 (VO); also elsewhere on the board
ENAB_GPS: R18.1, R20.2; also elsewhere on the board
GND: C19.2, C20.2, C22.2, C23.2, C26.2, C27.2, C28.2, R8.2, R11.1, R17.1, R18.2, R22.1, T1.2 (S), U5.1 (GND), U6.1 (GND), U8.P$5 (GND), U8.P$7 (FREQ), U8.P$11 (NC), U8.P$12 (NTC), U8.P$17 (GND), U9.P$1 (S2), U9.P$3 (TST), U9.P$4 (VSS); also elsewhere on the board
GPS_PWR: Q1.2 (S); also elsewhere on the board
I_BATT: U5.2 (OUT); also elsewhere on the board
I_SOLAR: U6.2 (OUT); also elsewhere on the board
L1_CHG: R8.1, R9.1, U8.P$16 (RUN)
L1_FAULTN: R16.1, U8.P$15 (~FAULT)
L1_PROG: R17.2, U8.P$13 (PROG)
LION1: C26.1, F1.1, R19.2, U8.P$9 (BAT), U8.P$10 (BATSNS)
unnamed: C18.1, L3.P$2, U7.10 (SW1), U7.11 (SW2)
unnamed: C28.1, R20.1, T1.3 (G)
unnamed: Q1.1 (G), R21.2, T1.1 (D)
unnamed: C18.2, U7.12 (VBST)
unnamed: C21.2, L4.P$1, U8.P$4 (SW)
unnamed: C21.1, U8.P$2 (BOOST)
unnamed: C20.1, U8.P$1 (INTVCC)
unnamed: R10.1, R11.2, U8.P$6 (MPPT)
unnamed: L4.P$2, U8.P$8 (CHGSNS)
unnamed: R15.1, U8.P$14 (~CHRG)
unnamed: C27.1, R19.1, U9.P$5 (VCC)
unnamed: C17.1, U7.14 (VCC)
unnamed: R22.2, U9.P$2 (CS)
unnamed: C25.1, R14.2, U7.3 (VREG5)
unnamed: C24.1, U7.4 (SS)
unnamed: R12.1, R13.2, U7.2 (VFB)
N_ENAB_REG: U7.7 (EN); also elsewhere on the board
PGOOD: R14.1, U7.6 (PG)
PWR_GND: C14.1, C15.1, C16.2, C17.2, C24.2, C25.2, R13.1, U7.5 (GND), U7.8 (PGND1), U7.9 (PGND2), U7.15 (EPAD)
VBATT: F1.2, R6.2, U5.4 (RS+); also elsewhere on the board
VREG_IN: C16.1, R6.1, U5.5 (RS-), U7.13 (VIN)
VSOLAR: D1.A, R7.2, U6.4 (RS+); also elsewhere on the board
VSOLAR_IN: C19.1, D1.C, R9.2, R10.2, U8.P$3 (IN)

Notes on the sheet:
Solar Panel Current Sensor
Battery Current Sensor
Zac Manchester, Max Holliday
GPS Power
FREQ tied to GND to select 750kHz switching frequency
R28 & R29 set Vmp=9V
2s2P Li-Ion Battery Charging Circuit
Run pulled up to ensure charging on startup
NTC tied to GND b/c no NTC sensor
LTC4121 can handle several amps of inrush current upon battery connection
NC tied to ground prevent charge buildup, approved by LT.
Ven threshold is 2.45V. Resistor divider sets RUN high when Solar Panel Voltage is >=6V.
Buck Converter - 3.3V OUT

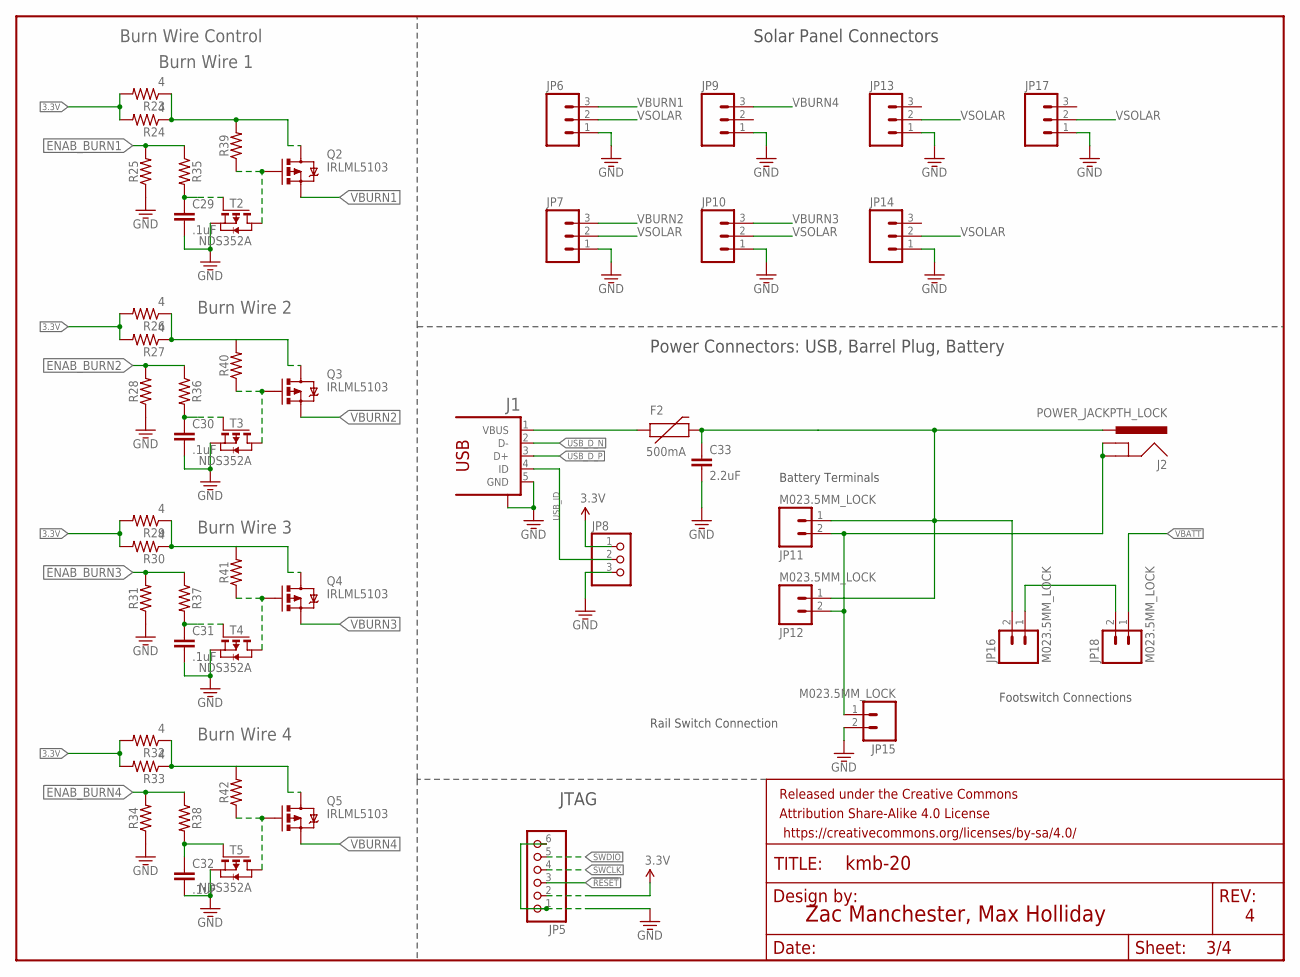
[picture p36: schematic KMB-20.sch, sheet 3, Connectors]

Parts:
C29, C30, C31, C32: .1uF; 0603-CAP@1
C33: 2.2uF; 0603
F2: 500mA; PTC-1206
FRAME3: FRAME-LETTER; CREATIVE_COMMONS
J1: 1981584-1
J2: POWER_JACKPTH_LOCK; POWER_JACK_PTH_LOCK
JP5: PINHD-1X6; 1X06
JP6, JP7, JP9, JP10, JP13, JP14, JP17: M03POLAR_LOCK; MOLEX-1X3_LOCK
JP8: PINHD-1X3; 1X03
JP11, JP12, JP15, JP16, JP18: M023.5MM_LOCK; SCREWTERMINAL-3.5MM-2_LOCK
Q2, Q3, Q4, Q5: IRLML5103; SOT23-3
R23, R24, R26, R27, R29, R30, R32, R33: 4; R0603
R25, R28, R31, R34, R35, R36, R37, R38, R39, R40, R41, R42: 0603
T2, T3, T4, T5: NDS352A; SOT-23

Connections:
3.3V: JP5.2, JP8.1, R23.2, R24.2, R26.2, R27.2, R29.2, R30.2, R32.2, R33.2; also elsewhere on the board
!RESET: JP5.3; also elsewhere on the board
ENAB_BURN1: R25.2, R35.1; also elsewhere on the board
ENAB_BURN2: R28.2, R36.1; also elsewhere on the board
ENAB_BURN3: R31.2, R37.1; also elsewhere on the board
ENAB_BURN4: R34.2, R38.1; also elsewhere on the board
GND: C29.2, C30.2, C31.2, C32.2, C33.2, J1.5 (GND), J1.S1, JP5.1, JP5.6, JP6.1, JP7.1, JP8.3, JP9.1, JP10.1, JP13.1, JP14.1, JP15.2, JP17.1, R25.1, R28.1, R31.1, R34.1, T2.2 (S), T3.2 (S), T4.2 (S), T5.2 (S); also elsewhere on the board
unnamed: JP16.1, JP18.2
unnamed: C30.1, R36.2, T3.3 (G)
unnamed: Q2.1 (G), R39.1, T2.1 (D)
unnamed: C31.1, R37.2, T4.3 (G)
unnamed: F2.1, J1.1 (VBUS)
unnamed: Q3.1 (G), R40.1, T3.1 (D)
unnamed: J2.GND, J2.GNDBREAK, JP11.2, JP12.2, JP15.1
unnamed: C29.1, R35.2, T2.3 (G)
unnamed: C32.1, R38.2, T5.3 (G)
unnamed: Q4.1 (G), R41.1, T4.1 (D)
unnamed: Q5.1 (G), R42.1, T5.1 (D)
SWCLK: JP5.4; also elsewhere on the board
SWDIO: JP5.5; also elsewhere on the board
USB_D_N: J1.2 (D-); also elsewhere on the board
USB_D_P: J1.3 (D+); also elsewhere on the board
USB_ID: J1.4 (ID), JP8.2
VBATT: C33.1, F2.2, J2.PWR, JP11.1, JP12.1, JP16.2, JP18.1; also elsewhere on the board
VBURN1: JP6.3, Q2.2 (S)
VBURN2: JP7.3, Q3.2 (S)
VBURN3: JP10.3, Q4.2 (S)
VBURN4: JP9.3, Q5.2 (S)
VBURN_IN: Q2.3 (D), Q3.3 (D), Q4.3 (D), Q5.3 (D), R23.1, R24.1, R26.1, R27.1, R29.1, R30.1, R32.1, R33.1, R39.2, R40.2, R41.2, R42.2
VSOLAR: JP6.2, JP7.2, JP10.2, JP13.2, JP14.2, JP17.2; also elsewhere on the board

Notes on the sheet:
Footswitch Connections
Solar Panel Connectors
Battery Terminals
Rail Switch Connection
Zac Manchester, Max Holliday
JTAG
Power Connectors: USB, Barrel Plug, Battery
Burn Wire 1
Burn Wire Control
Burn Wire 2
Burn Wire 3
Burn Wire 4

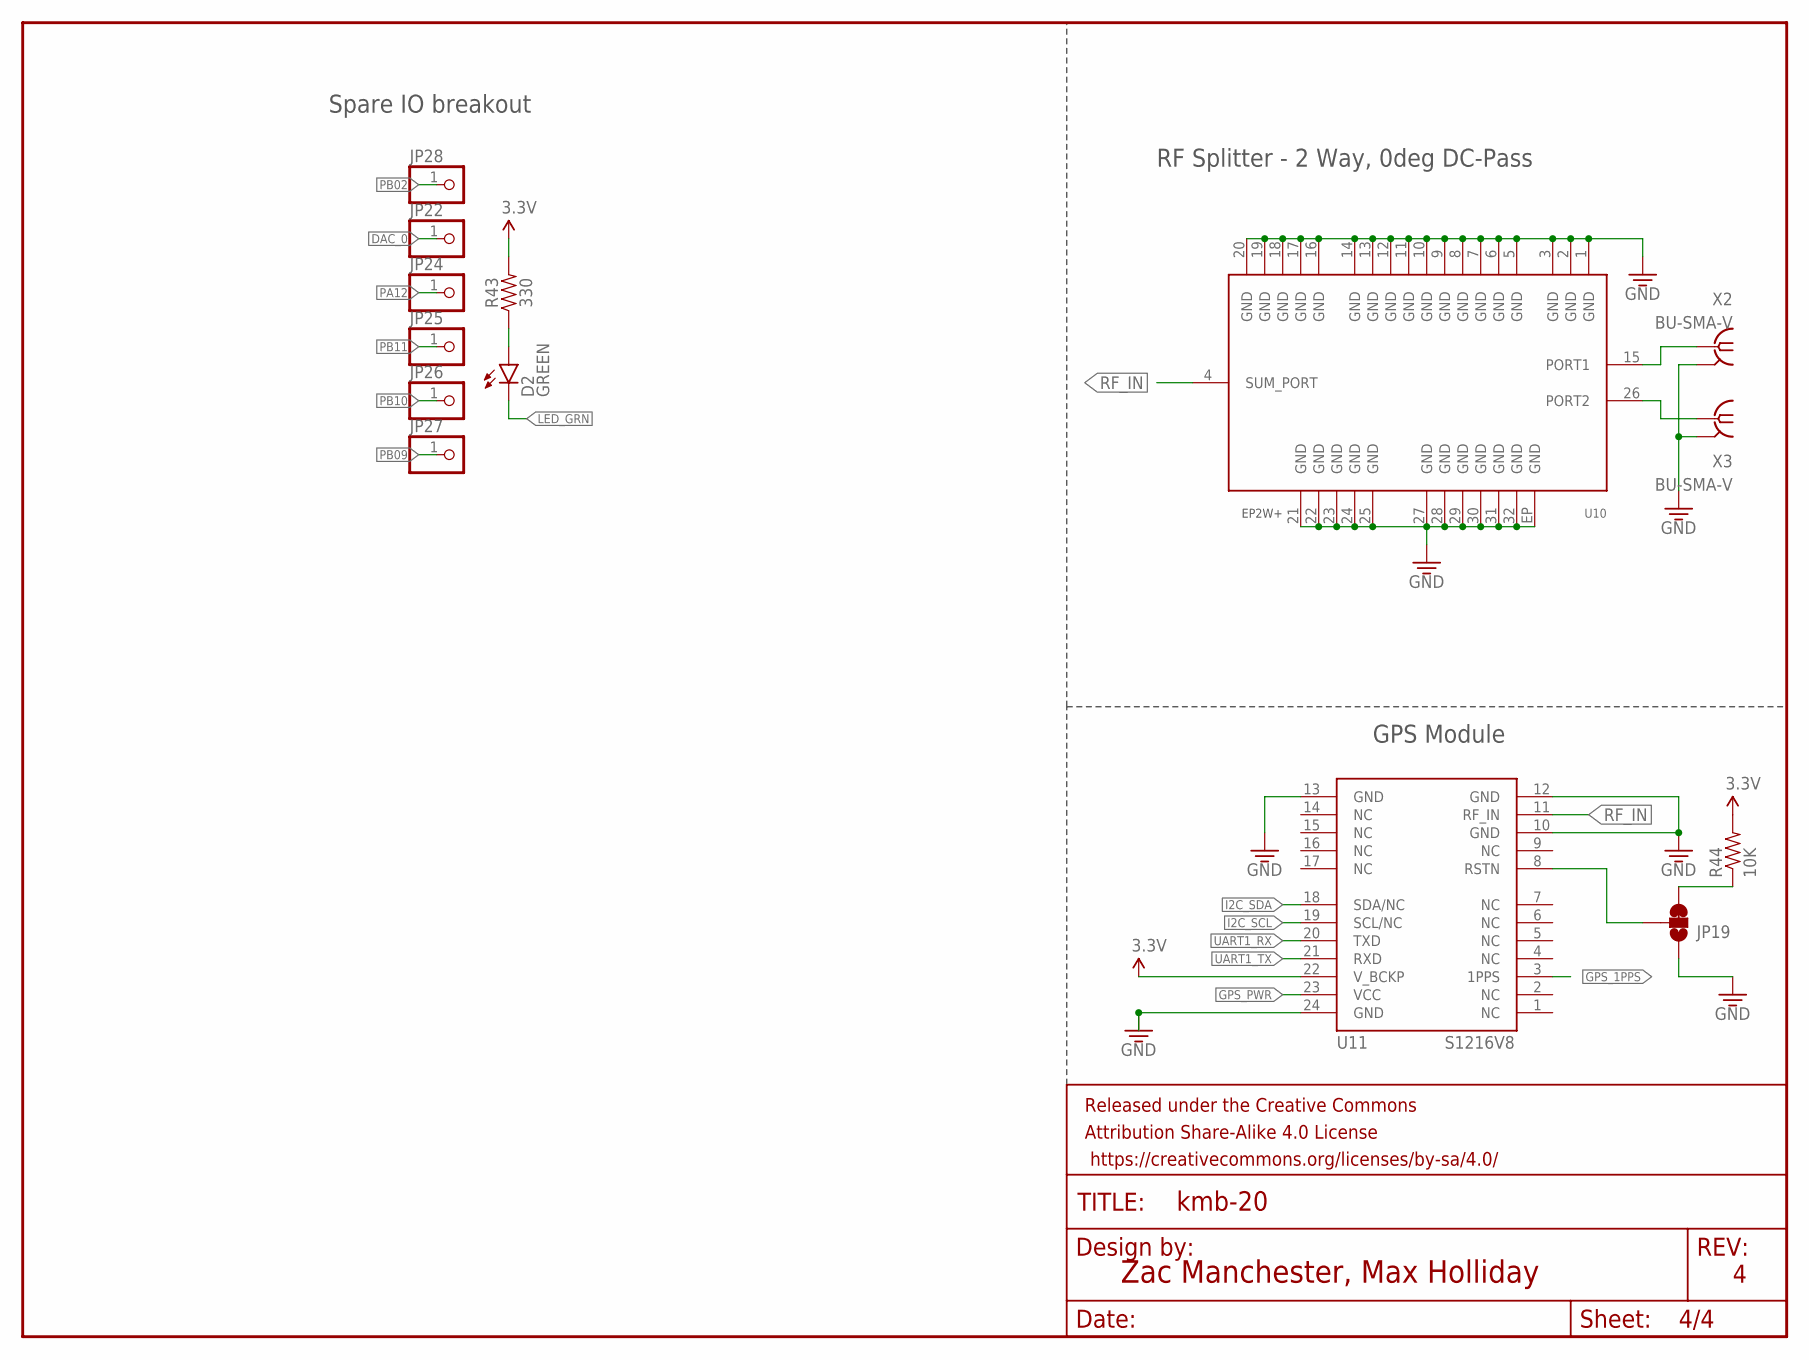
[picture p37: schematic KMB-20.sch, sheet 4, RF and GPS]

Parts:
D2: GREEN; LED-0603
FRAME4: FRAME-LETTER; CREATIVE_COMMONS
JP19: JUMPER-PAD-3-2OF3_NC_BY_TRACE_SMALL; PAD-JUMPER-3-2OF3_NC_BY_TRACE_YES_SILK_FULL_BOX
JP22, JP24, JP25, JP26, JP27, JP28: PINHD-1X1; 1X01
R43: 330; 0603-RES
R44: 10K; 0603-RES
U10: EP2W+; QFN32-5X5MM
U11: S1216V8; S1216_24PIN_PACKAGE
X2, X3: BU-SMA-V

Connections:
3.3V: R43.2, R44.2, U11.22 (V_BCKP); also elsewhere on the board
DAC_0: JP22.1; also elsewhere on the board
GND: JP19.1, U10.1 (GND), U10.2 (GND), U10.3 (GND), U10.5 (GND), U10.6 (GND), U10.7 (GND), U10.8 (GND), U10.9 (GND), U10.10 (GND), U10.11 (GND), U10.12 (GND), U10.13 (GND), U10.14 (GND), U10.16 (GND), U10.17 (GND), U10.18 (GND), U10.19 (GND), U10.20 (GND), U10.21 (GND), U10.22 (GND), U10.23 (GND), U10.24 (GND), U10.25 (GND), U10.27 (GND), U10.28 (GND), U10.29 (GND), U10.30 (GND), U10.31 (GND), U10.32 (GND), U10.EP (GND), U11.10 (GND), U11.12 (GND), U11.13 (GND), U11.24 (GND), X2.2, X2.3 (2), X2.4 (2), X2.5 (2), X3.2, X3.3 (2), X3.4 (2), X3.5 (2); also elsewhere on the board
GPS_1PPS: U11.3 (1PPS); also elsewhere on the board
GPS_PWR: U11.23 (VCC); also elsewhere on the board
I2C_SCL: U11.19 (SCL/NC); also elsewhere on the board
I2C_SDA: U11.18 (SDA/NC); also elsewhere on the board
LED_GRN: D2.C; also elsewhere on the board
unnamed: D2.A, R43.1
unnamed: JP19.2, U11.8 (RSTN)
unnamed: U10.15 (PORT1), X2.1
unnamed: U10.26 (PORT2), X3.1
unnamed: JP19.3, R44.1
PA12: JP24.1; also elsewhere on the board
PB02: JP28.1; also elsewhere on the board
PB09: JP27.1; also elsewhere on the board
PB10: JP26.1; also elsewhere on the board
PB11: JP25.1; also elsewhere on the board
RF_IN: U10.4 (SUM_PORT), U11.11 (RF_IN)
UART1_RX: U11.20 (TXD); also elsewhere on the board
UART1_TX: U11.21 (RXD); also elsewhere on the board

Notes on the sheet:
GPS Module
RF Splitter - 2 Way, 0deg DC-Pass
Zac Manchester, Max Holliday
Spare IO breakout

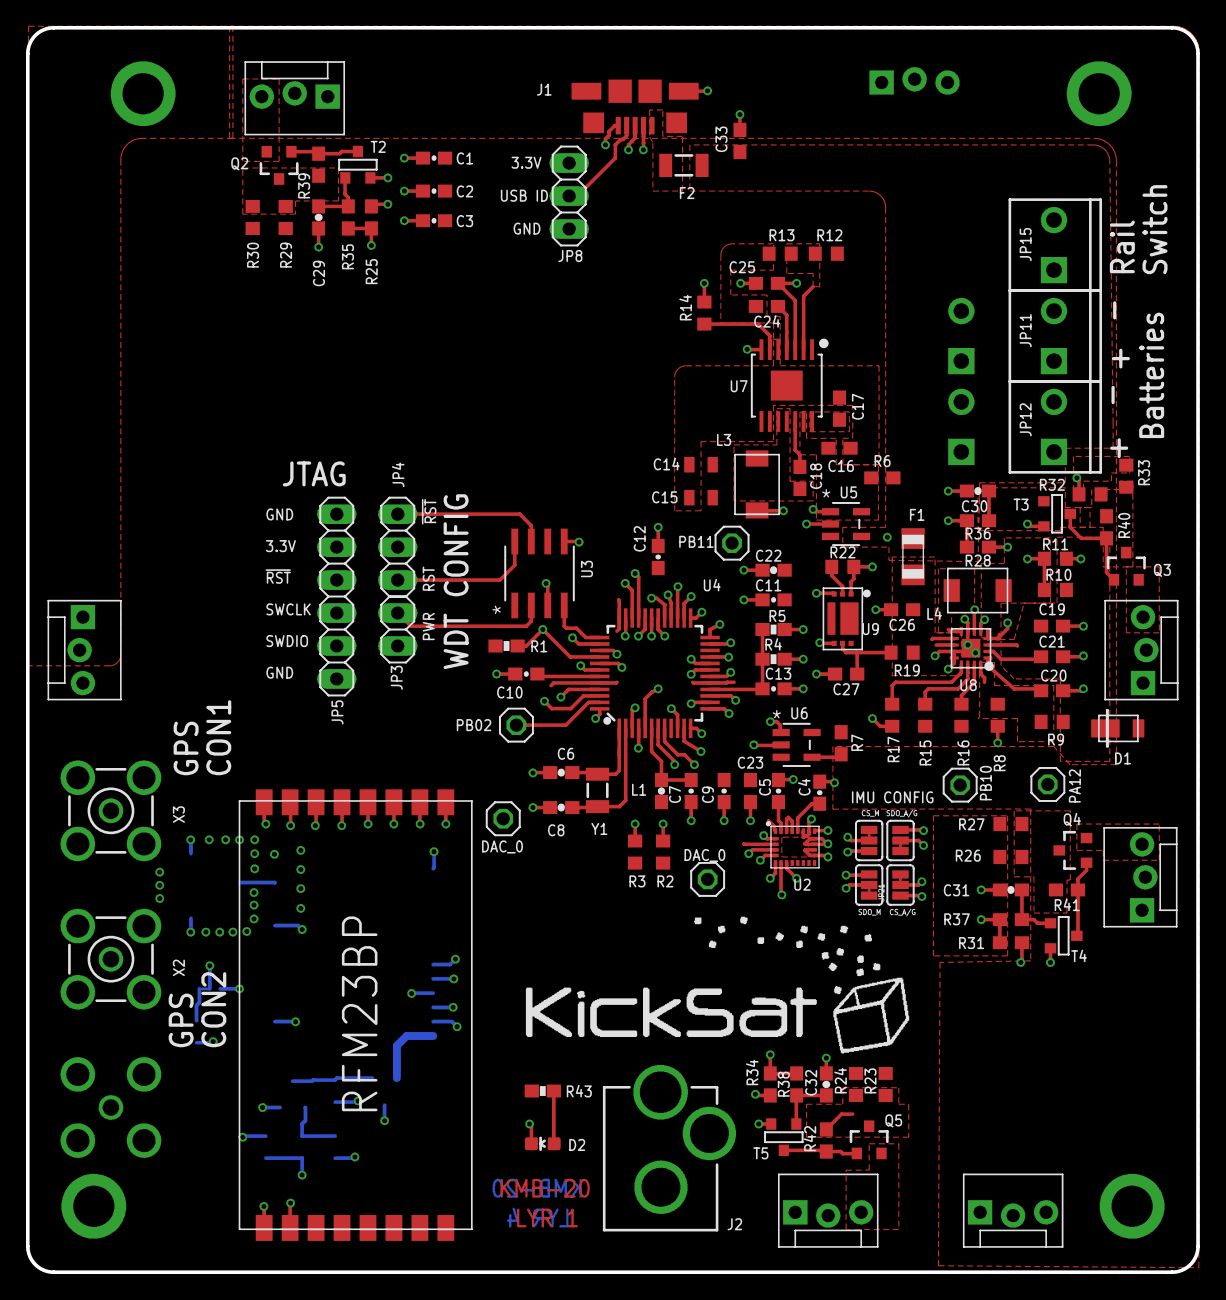
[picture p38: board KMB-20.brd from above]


Board: 4 copper layers, 90.2 x 95.9 mm, 144 parts (15 on the bottom side), 100 nets.

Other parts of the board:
L5: KICKSAT_LOGO

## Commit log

2018-04-11 Initial commit of new KickSat-2 board
    [Mainbaord.brd, Mainboard.sch]
2018-06-01 Latest kicksat2 mainboard update (KMB-21). New from KMB-20: MRAM, power relays, microSD card, 2 spots for [XLab Tester Boards](https://github.com/maholli/XTB)
    [Mainboard.sch, mainboard.brd]
2018-06-07 adding KMB-21 BOM
    [KMB-21 BOM.xlsx]
2018-06-26 ensuring latest
    [mainboard.brd, mainboard.sch]
2018-06-26 adding pdf of schematic
2018-06-27 added schematic
2018-07-10 Motherboard IMU
2018-07-10 Add files via upload
    Editable version of the conops diagram as a powerpoint
2018-07-25 added KMB-22 design
    [KMB-20.brd, KMB-20.sch, KMB-21.brd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]
2018-07-25 fixed schematic output error
2018-07-25 updated schematic export errors
2018-07-25 KMB-22 schematic update
2018-07-25 changed solar panel connector on KMB-22
    [KMB-22.brd, KMB-22.sch]
2018-07-28 KMB-20 schematic
2018-08-13 fixing folder name
    [KMB-22.brd, KMB-22.sch]
2018-08-15 adding missing schematic pages
2018-08-22 added KMB-23
    [KMB-23.brd, KMB-23.sch]
2018-08-22 updated mainboard to KMB-23
    [mainboard.brd, mainboard.sch]
2018-09-19 added KMB-24
    [KMB-24.brd, KMB-24.sch]

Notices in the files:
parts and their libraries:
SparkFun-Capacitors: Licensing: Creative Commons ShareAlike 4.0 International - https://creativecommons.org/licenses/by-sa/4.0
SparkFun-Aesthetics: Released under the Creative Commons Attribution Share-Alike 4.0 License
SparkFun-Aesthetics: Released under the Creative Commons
